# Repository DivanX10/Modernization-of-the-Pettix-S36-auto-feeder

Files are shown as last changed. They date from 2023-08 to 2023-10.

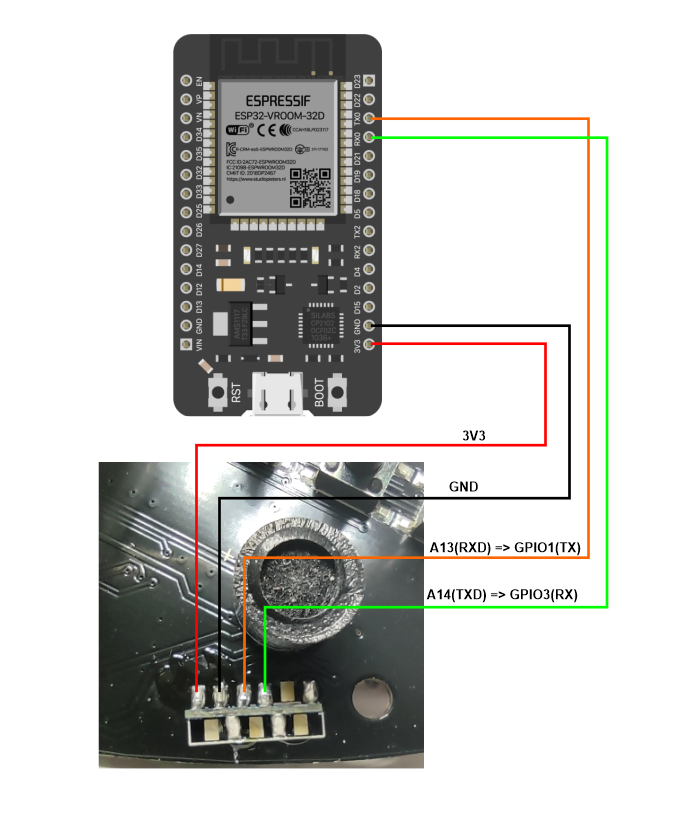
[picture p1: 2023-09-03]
images/Connect the ESP to the RX-TX feeder.png

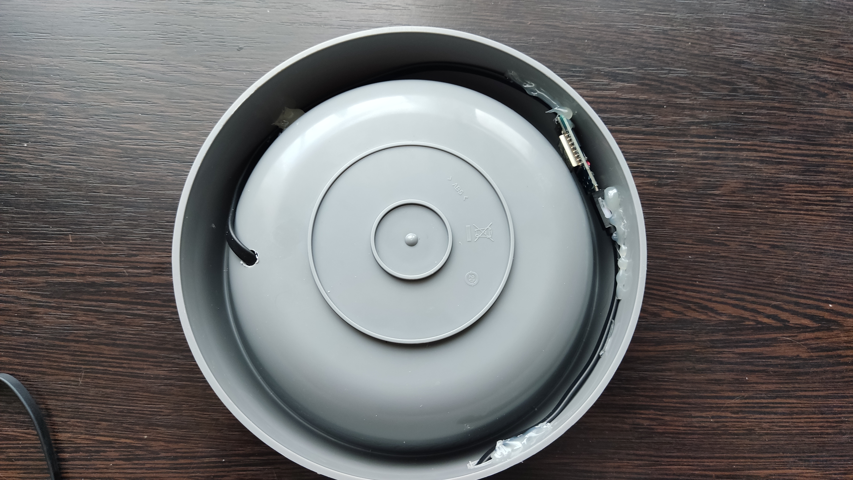
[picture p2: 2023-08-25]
images/Images 04.jpg

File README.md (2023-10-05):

### [Read in English here](https://github.com/DivanX10/cat-bowl-with-scales/blob/main/README_EN.md)

# Модернизация автокормушки Pettix S36

Проект для ESPHome и Home Assistant



***

### Смотреть видео [Автокормушка с миской на весах](https://youtu.be/qWqOF85e7Kk)
### Смотреть видео [Автокормушка с вращающейся миской на весах](https://youtu.be/ATh8qVqtzHo?si=UaMHs_tmDmoli1Qk)

***

## Отвязываем кормушку от облака Tuya и переводим на ESPHome

<details>
  <summary><b>Подключаем ESP к кормушке</b></summary>

  > Используйте платы ESP8266 и ESP32 на свое усмотрение, я использовал ESP32 по той причине, что оно у меня было свободным
 
Выпаиваем чип WBR2 и подключаем ESP. [WBR2 Module Datasheet](https://developer.tuya.com/en/docs/iot/wbr2-datasheet?id=K989h4vonmsey)





  
</details>

<details>
  <summary><b>Расшифровка протокола для управления кормушкой</b></summary>

**Включить меделенную подачу корма**
```
55:AA:00:06:00:05:06:01:00:01:01:13
```

**Выключить меделенную подачу корма**
```
55:AA:00:06:00:05:06:01:00:01:00:12
```
***

**Включить 24 часа**
```
55:AA:00:06:00:05:66:01:00:01:01:73
```

**Выключить 24 часа**
```
55:AA:00:06:00:05:66:01:00:01:00:72
```
***

**Подача порции корма**

1 порция
```
55:AA:00:06:00:08:03:02:00:04:00:00:00:01:17
```

2 порции
```
55:AA:00:06:00:08:03:02:00:04:00:00:00:02:18
```

3 порции
```
55:AA:00:06:00:08:03:02:00:04:00:00:00:03:19
```

4 порции
```
55:AA:00:06:00:08:03:02:00:04:00:00:00:04:1A
```

5 порции
```
55:AA:00:06:00:08:03:02:00:04:00:00:00:05:1B
```

6 порции
```
55:AA:00:06:00:08:03:02:00:04:00:00:00:06:1C
```

***

**Время воспроизведения голоса**

0
```
55:AA:00:06:00:08:12:02:00:04:00:00:00:00:25
```

1
```
55:AA:00:06:00:08:12:02:00:04:00:00:00:01:26
```

2
```
55:AA:00:06:00:08:12:02:00:04:00:00:00:02:27
```

3
```
55:AA:00:06:00:08:12:02:00:04:00:00:00:03:28
```

4
```
55:AA:00:06:00:08:12:02:00:04:00:00:00:04:29
```

5
```
55:AA:00:06:00:08:12:02:00:04:00:00:00:05:2A
```

6
```
55:AA:00:06:00:08:12:02:00:04:00:00:00:06:2B
```

***

**Сенсор наличия корма в баке**

В контейнере корм имеется
```
55:AA:03:07:00:05:0E:05:00:01:00:22
```

В контейнере корм закончился
```
55:AA:03:07:00:05:0E:05:00:01:01:23
```

</details>

</details>

<details>
  <summary><b>ESPHome</b></summary>

### Конфигурации смотреть [здесь](https://github.com/DivanX10/Modernization-of-the-Pettix-S36-auto-feeder/tree/main/files/ESPHome/ru)
***  
Перед тем как использовать весь код, откалибруйте свои весы. Уберите из кода эти строчки и включите журналирование в режиме DEBUG. Так мы будем получать сырые данные. Зафиксируйте вес без груза, скопируйте цифры с логов как есть, потом возъмите груз на 500 грамм и поставьте на весы, зафиксируйте цифры. Все эти цифры запишите в линейный фильтр

Пример фильтра, где `-169085` это сырое значение и это значение без груза на весах, поэтому я указал что данное значение имеет вес 0 грамм, а значение `-92230` отобразилось в логах после того, как я установил груз весом 500 грамм и после указал, что данное значение имеет вес 500 грамм
```
filters:
  - calibrate_linear:
      - -169085 -> 0
      - -92230 -> 500
```

Так выглядит код с журналированием в режиме отладки и без использования фильтра с линейной калибровкой. Это позволит вам получить сырые значения
```
#Журналирование
logger:
  level: DEBUG #Режим отладки

sensor:
  # Весы кошачьей миски
  - platform: hx711
    name: "${node_name} Weight"
    icon: mdi:scale
    id: idWeight
    dout_pin: D7 #DT
    clk_pin: D6  #SCK
    gain: 64
    update_interval: 1s
    unit_of_measurement: g
    accuracy_decimals: 0
    device_class: weight
    state_class: measurement
    entity_category: diagnostic
    internal: False
```

Если показания нестабильны, часто и сильно скачут, то смените контроллер HX711 на исправный, в противном случае фильтры не помогут. Лично сам с этим столкнулся и много времени потратил впустую на настройку фильтров. При исправном контроллере HX711 показания весов в момент покоя могут чуть-чуть меняться и это нормально, но не скачут сильно и постоянно. В таком случае дополнительный фильтр поможет, например фильтр медиана, который сможет стабилизировать показания весов. [Подробнее читаем в документации ESPHome](https://esphome.io/components/sensor/index.html#median)

```
      - median:
          window_size: 7
          send_every: 4
          send_first_at: 3
```
                
</details>

## Автокормушка с миской на весах

<details>
  <summary><b>Что нужно для сборки весов для миски</b></summary>
  
* Чувствительные тензодатчики с точностью 1 грамм. Найти можно в электронных кухонных весах с круглыми ножками. Берем любые кухонные весы с круглыми ножками, а не с палками. Это легко можно понять, если перевернуть весы. [Я брал такие кухонные весы](https://ozon.ru/t/zewBN6W)
* ESP8266 Wemos Mini D1
* Контроллер весов HX711
* Распечатать платформу. Скачать можно [здесь](https://github.com/DivanX10/cat-bowl-with-scales/tree/main/files/STL%20Scales)
</details>

<details>
  <summary><b>Фотографии</b></summary>
  





</details>

<details>
  <summary><b>Схема подключения и сборка</b></summary>

Схема подключения весов к контроллеру HX711 и к ESP8266







</details>

<details>
  <summary><b>Home Assistant</b></summary>

feeder_pettix_s36_control_panel_scales_ru

**Для работы карточки необходимо установить компоненты**
* [Fold Entity Row](https://github.com/thomasloven/lovelace-fold-entity-row)
* [Multiple Entity Row](https://github.com/benct/lovelace-multiple-entity-row)

**Карточка и шаблоны**
* Код карточки можно взять [здесь](https://github.com/DivanX10/Modernization-of-the-Pettix-S36-auto-feeder/blob/main/files/HomeAssistant/ru/Карточка.%20Миска%20с%20весами.yaml)
* Код шаблона можно взять [здесь](https://github.com/DivanX10/Modernization-of-the-Pettix-S36-auto-feeder/blob/main/files/HomeAssistant/ru/Шаблон.yaml)
  
</details>

<details>
  <summary><b>3D модель</b></summary>
  
Платформу спроектировал в программе FreeCAD. Скачать FreeCAD [можно здесь](https://www.freecad.org/?lang=ru). Я вложил 3 файла, два файла STL и один для FreeCAD, где вы сможете отредактировать при необходимости. Я спроектировал так, чтобы тензодатчики держались крепко и сделал клипсы в виде дуги из-за чего тензодатчики с трудом встают на свои места, нужно тоненькой плоской отверткой поддеть, но зато стоят четко и очень трудно их будет демонтировать без повреждения корпуса.

Готовые модели можно скачать [здесь](https://github.com/DivanX10/Modernization-of-the-Pettix-S36-auto-feeder/tree/main/files/STL%20Scales)



</details>

## Автокормушка с вращающейся миской с весами

<details>
  <summary><b>Что нужно для сборки вращающейся миски с весами</b></summary>
  
* Чувствительные тензодатчики с точностью 1 грамм. Найти можно в электронных кухонных весах с круглыми ножками. Берем любые кухонные весы с круглыми ножками, а не с палками. Это легко можно понять, если перевернуть весы. [Я брал такие кухонные весы](https://ozon.ru/t/zewBN6W)



* ESP8266 Wemos Mini D1
* Контроллер весов HX711
* Модуль драйвера ULN2003 и шаговый двигатель 28YBJ 48
* Модуль часов реального времени (RTS) DS1307
* Подшипник 6814 2RS (61814) SLZ. Брал [здесь](https://ozon.ru/t/6M8ZB3Y)
  * Внешний диаметр: 90 мм
  * Внутренний диаметр: 70 мм
  * Высота: 10 мм


* Жидкая резина KUDO COLOR FLEX, Прозрачная. Брал [здесь](https://ozon.ru/t/wz6gR7n)
  


* Распечатать миску и платформу. Скачать можно [здесь](https://github.com/DivanX10/Modernization-of-the-Pettix-S36-auto-feeder/tree/main/files/STL%20Rotating%20bowl%20with%20scales)

</details>

<details>
  <summary><b>Фотографии</b></summary>
  








</details>

<details>
  <summary><b>Cхема подключения</b></summary>

Питание берем от самой автокормушки, которое выдает 5V и 1A, чего будет достаточно, чтобы запитать всю кормушку полностью. Для полной работы кормушки требуется сила тока до 800мА

Connection diagram 01

</details>

<details>
  <summary><b>Home Assistant</b></summary>

feeder_pettix_s36_control_panel_ru

**Для работы карточки необходимо установить компоненты**
* [History explorer card](https://github.com/alexarch21/history-explorer-card)
* [Button Card](https://github.com/custom-cards/button-card)

**Карточка и шаблоны**
* Код карточки можно взять [здесь](https://github.com/DivanX10/Modernization-of-the-Pettix-S36-auto-feeder/blob/main/files/HomeAssistant/ru/Карточка.%20Вращающаяся%20миска%20с%20весами.yaml)
* Код шаблона можно взять [здесь](https://github.com/DivanX10/Modernization-of-the-Pettix-S36-auto-feeder/blob/main/files/HomeAssistant/ru/Шаблон.yaml)

</details>

<details>
  <summary><b>3D модель</b></summary>

Миска состоит из нескольких деталей. Сделано для экономии времени печати и филамента на случай, если деталь сломалась и чтобы не печатать всю миску целиком заново. Про подшипник 6814 2RS (61814) SLZ читаем ниже 

Готовые модели можно скачать [тут](https://github.com/DivanX10/Modernization-of-the-Pettix-S36-auto-feeder/tree/main/files/STL%20Rotating%20bowl%20with%20scales)



> Оранжевый круг, это подшипник 6814 2RS (61814) SLZ, который вставляется в круглую платформу под стальную миску (на скриншоте синего цвета). Чтобы стальная миска не скользила на верхней части платформы, рекомендую сделать напыление жидкой резиной. Получается отличное сцепление с миской



</details>

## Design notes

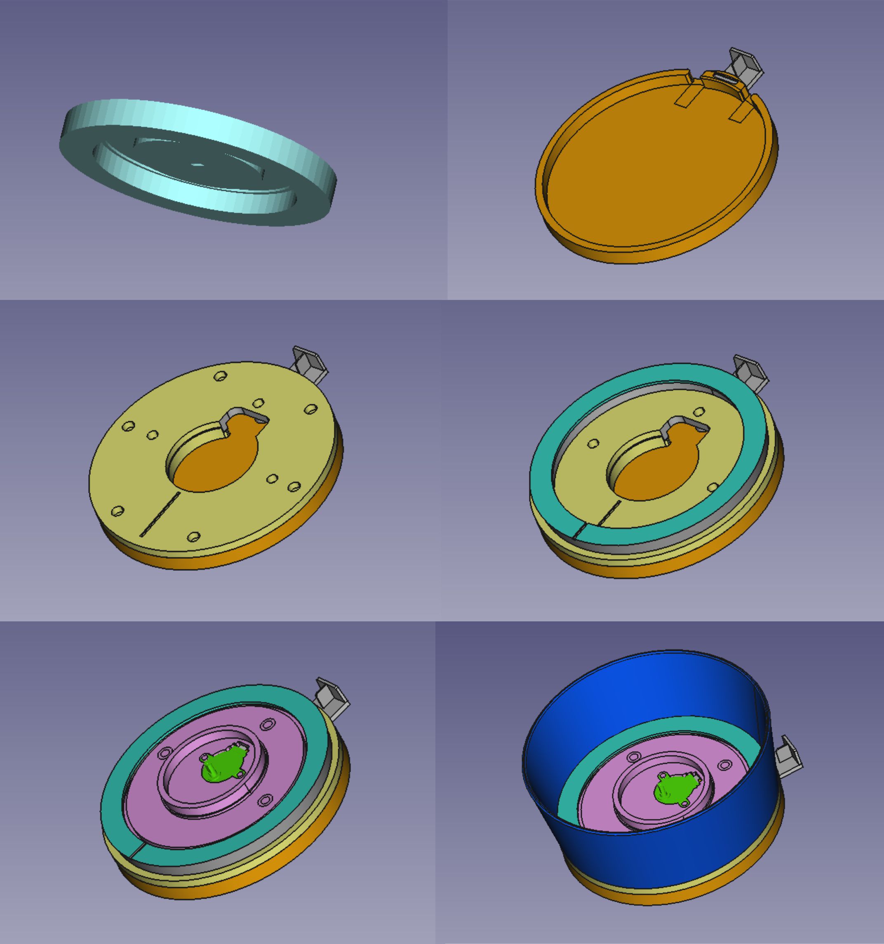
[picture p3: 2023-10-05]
images/3d model rotating bowl with scales 01.jpg

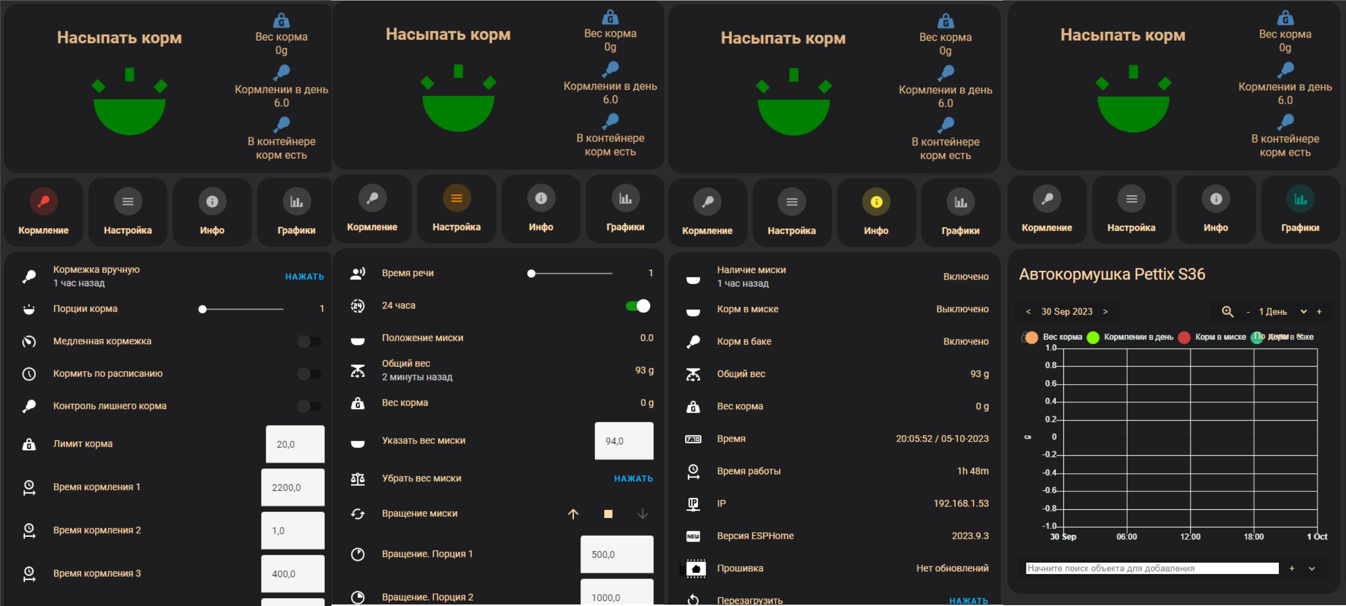
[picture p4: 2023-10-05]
images/feeder pettix s36 control panel rotating bowl with scales ru.jpg

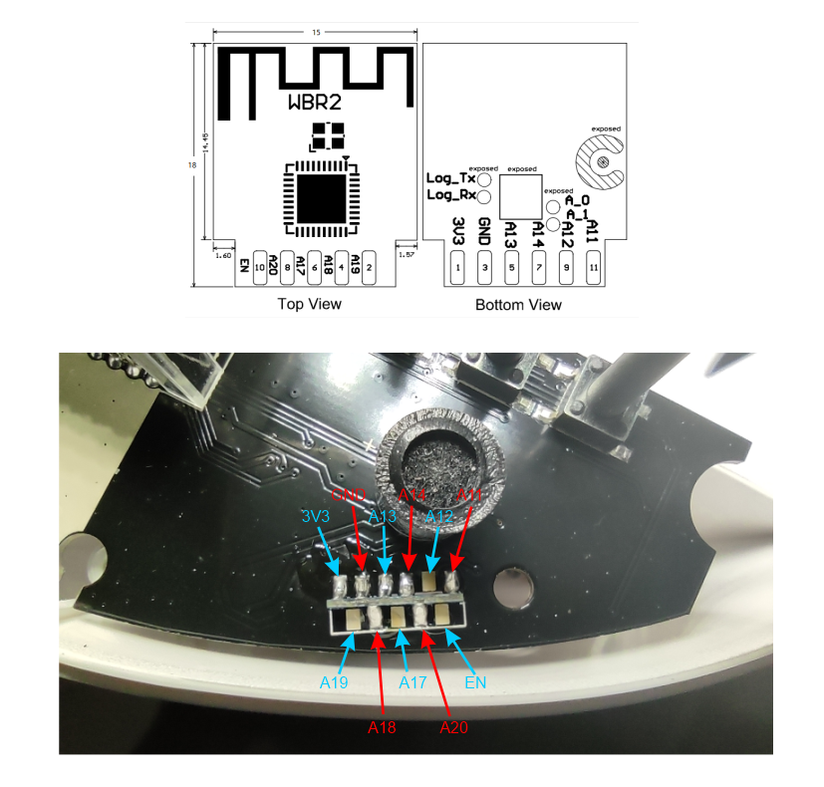
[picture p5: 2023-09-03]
images/Images 07.png

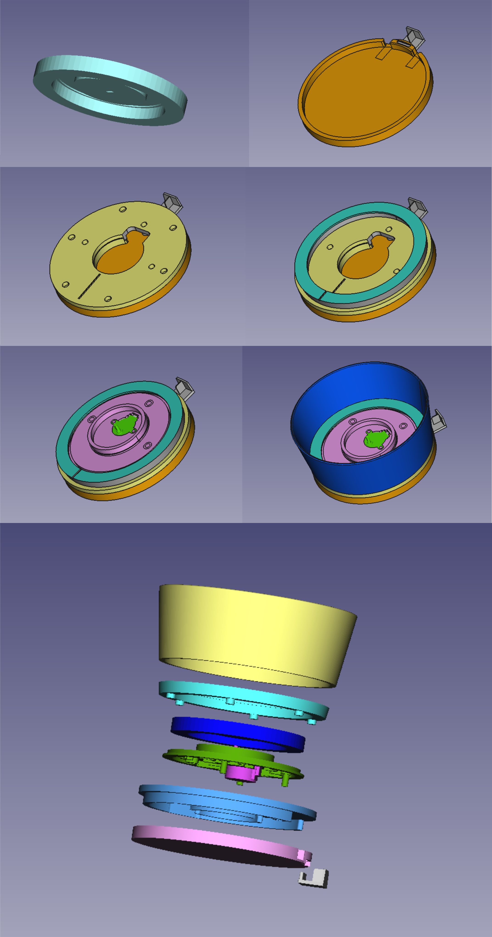
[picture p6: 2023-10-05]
images/3d model rotating bowl with scales.jpg

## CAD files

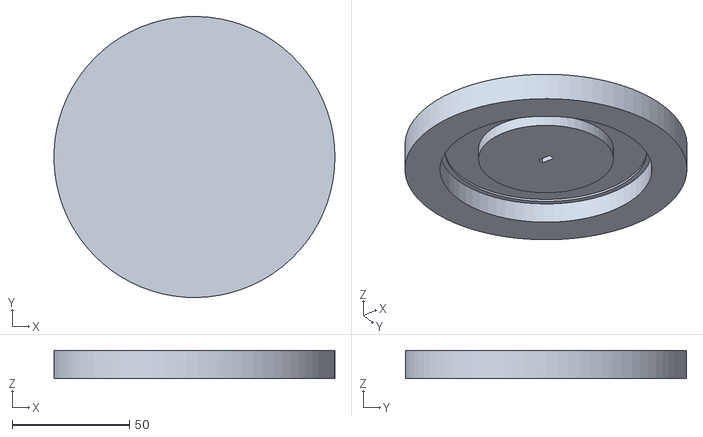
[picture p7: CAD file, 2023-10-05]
files/STL Rotating bowl with scales/08 Upper platform for bowl and bearing (Print 1 piece).stl
120.0 x 120.0 x 12.0

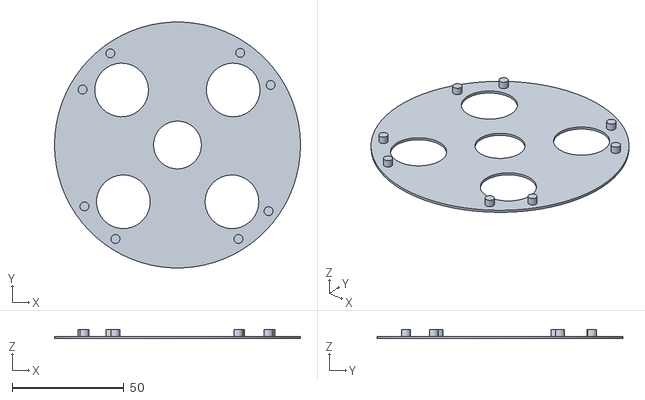
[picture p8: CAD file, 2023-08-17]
files/STL Scales/Cap.stl
110.0 x 109.9 x 4.10

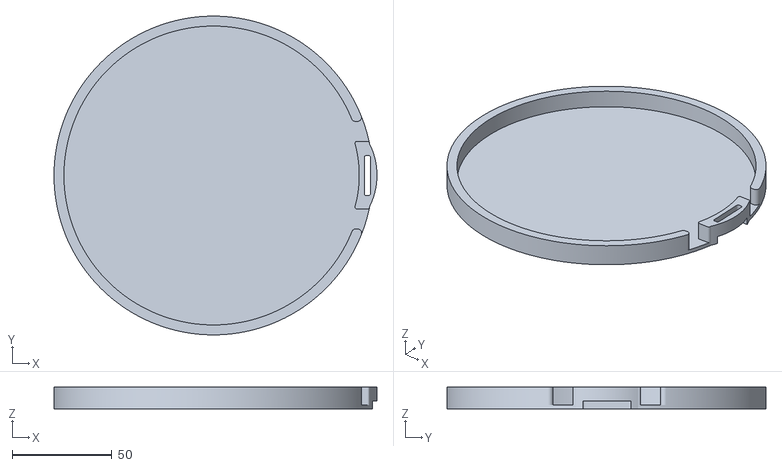
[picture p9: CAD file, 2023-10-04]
files/STL Rotating bowl with scales/05 Lower cover for the middle platform (Print 1 piece).stl
162.1 x 160.0 x 11.0

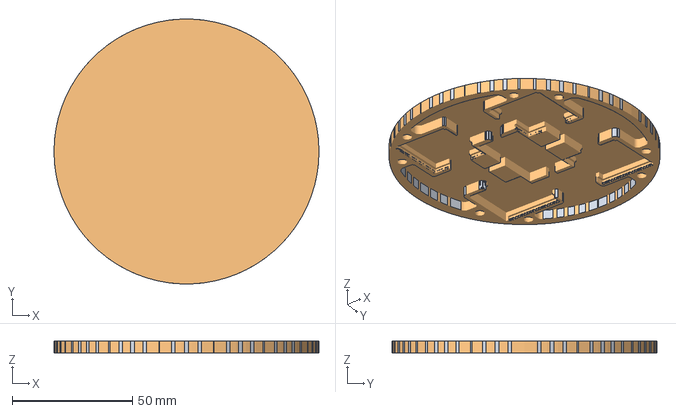
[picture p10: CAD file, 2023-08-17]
files/STL Scales/Platform for a bowl.FCStd
110.0 x 110.0 x 5.00 mm
Круглая платформа005
Круглая платформа005 (Meshed)

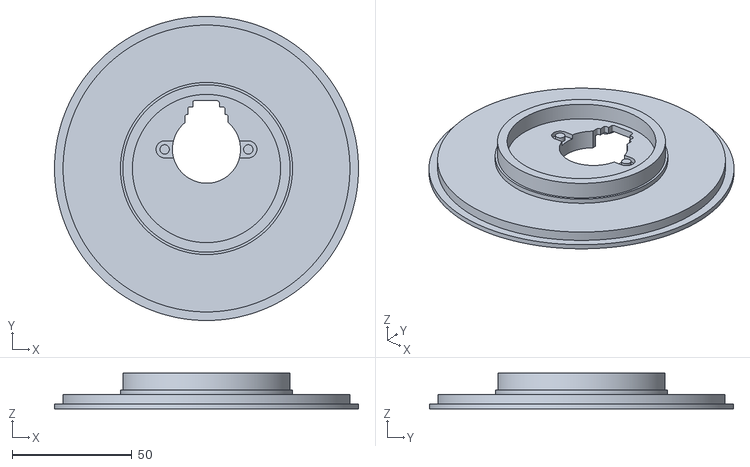
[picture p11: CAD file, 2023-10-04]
files/STL Rotating bowl with scales/03 Platform with scales and motor (Print 1 piece).stl
127.2 x 127.2 x 15.0

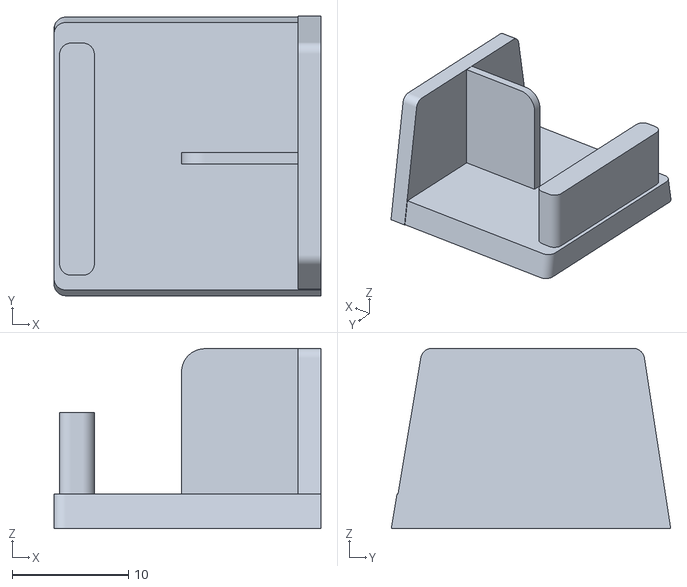
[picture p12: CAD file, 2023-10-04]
files/STL Rotating bowl with scales/06 Feeder bowl holder (Print 1 piece).stl
23.0 x 24.1 x 15.5

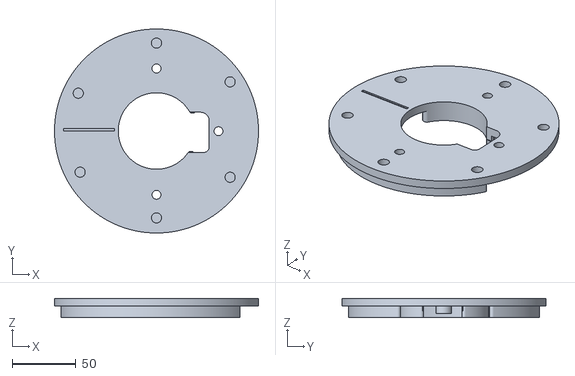
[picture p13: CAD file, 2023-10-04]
files/STL Rotating bowl with scales/04 Medium platform for a platform with weights (Print 1 piece).stl
160.0 x 160.0 x 15.0

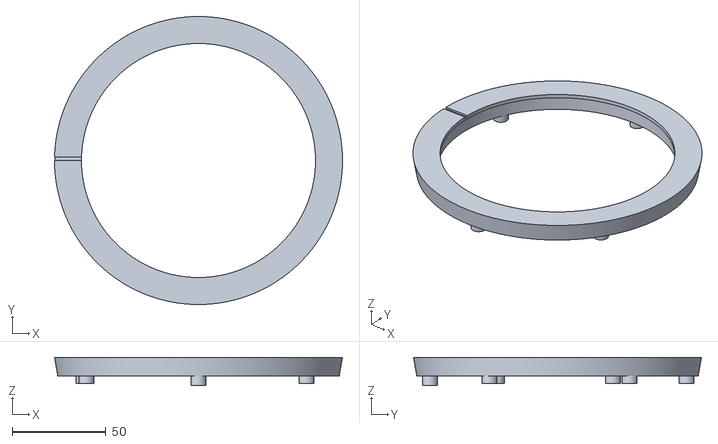
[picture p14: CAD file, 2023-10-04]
files/STL Rotating bowl with scales/02 Lock with axes for the upper body and platform with scales (Print 1 piece).stl
153.9 x 153.9 x 15.0

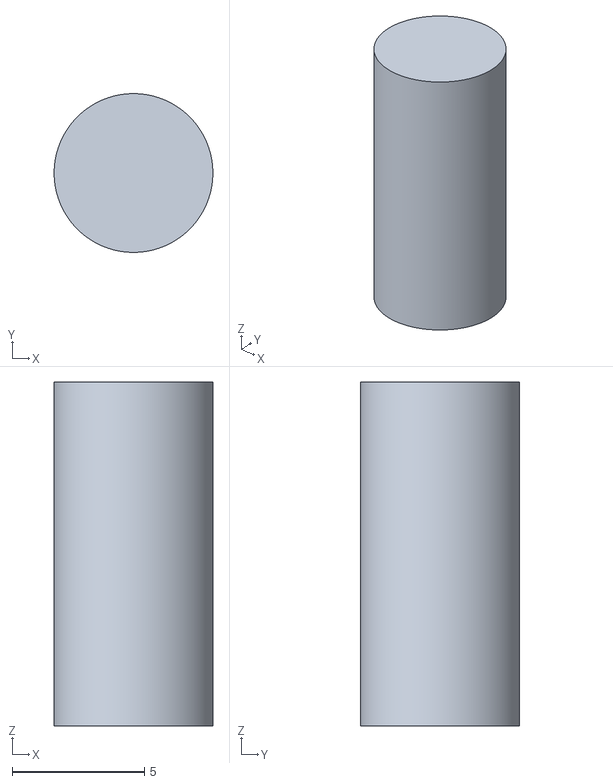
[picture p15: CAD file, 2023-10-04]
files/STL Rotating bowl with scales/07 Cylinder (Print 3 pieces).stl
6.00 x 6.00 x 13.0

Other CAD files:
files/STL Scales/Platform for a bowl.stl

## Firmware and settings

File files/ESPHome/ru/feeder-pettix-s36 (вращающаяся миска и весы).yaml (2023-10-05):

#####################################################################################
##################################### Переменные ####################################
substitutions:
  board_name: ESP Feeder Pettix S36
  node_name: feeder pettix s36
  max_skipped_time: "60" #Минуты, в течение которых будем запускать пропущенную кормежку

#####################################################################################
################################ Основная конфигурация ##############################
esphome:
  name: feeder-pettix-s36
  friendly_name: feeder-pettix-s36
  comment: WeMos D1 Feeder Pettix S36
  on_boot:
    then:
      #Считаем время RTC один раз при загрузке системы.
      ds1307.read_time:

#####################################################################################
###################################### Платформа ####################################
esp8266:
  board: d1_mini
  framework:
    version: recommended
  #Сохраняем предустановленные настройки. После перезагрузки настройки не сбрасываются  
  restore_from_flash: true

#Сброс данных на флэш-накопитель для уменьшения износа флеш-накопителя
preferences:
  flash_write_interval: 1min

#####################################################################################
################################ Wi-Fi и точка доступа ##############################
#Учетные данные Wi-Fi для подключения платы к домашней сети
wifi:
  ssid: !secret wifi_ssid
  password: !secret wifi_password
  id: idWiFi
  fast_connect: off
  reboot_timeout: 5min

#Если не будет связи с WiFi, то поднимется точка доступа
  ap:
    ssid: ESP Feeder S36 Tuya
    password: !secret ap_esp_password
    ap_timeout: 1 min
    manual_ip:
      static_ip: 192.168.4.1
      gateway: 192.168.4.1
      subnet: 255.255.255.0

#Компонент mdns заставляет узел объявлять о себе в локальной сети, используя протокол многоадресной рассылки DNS (mDNS), по умолчанию для mDNS disabled: false
mdns:
  disabled: false

#Компонент captive portal в ESPHome является резервным механизмом на случай сбоя подключения к настроенному Wi-Fi
captive_portal:

#Веб сервер
web_server:
  port: 80

#Журналирование
logger:
  level: ERROR #DEBUG
  baud_rate: 0

#Enable Home Assistant API
#Шифрование выключил
api:

#Обновление по воздуху (OTA)
ota:
  password: "esphome"

#####################################################################################
######################################### UART ######################################
uart:
  tx_pin: GPIO1 #белый провод
  rx_pin: GPIO3 #зеленый провод
  baud_rate: 9600
  stop_bits: 1
  data_bits: 8
  parity: NONE

#Включить компонент Tuya MCU
tuya:
  time_id: homeassistant_time
  on_datapoint_update:
    - sensor_datapoint: 14
      datapoint_type: bitmask
      then:
        lambda: |-
          std::bitset<4> probes(x);
          probes.flip();
          id(idFoodLevel).publish_state(probes.test(0));

#####################################################################################
########################### Глобальные переменные ###################################
globals:
#Последняя кормежка по расписанию
  - id: last_manual_feed_ts
    type: int
    restore_value: yes
    initial_value: '2147483648'

  - id: idWeightBowlGlobal
    type: int
    restore_value: yes
    initial_value: '0'

#####################################################################################
############################# Платформа вывода ######################################
#Шаговый мотор 28BYJ-48
stepper:
  - platform: uln2003
    id: idStepperMotor
    pin_a: D5
    pin_b: D6
    pin_c: D7
    pin_d: D8
    max_speed: 250 steps/s
    sleep_when_done: True
    step_mode: FULL_STEP

    #Опционально:
    acceleration: inf
    deceleration: inf

#Модуль часов реального времени (RTS) на базе микросхемы DS1307
i2c:
  sda: D1 #синий провод
  scl: D2 #зеленый провод
  scan: true
  id: ds1307_time

#####################################################################################
################################## Выключатель ######################################
switch:
#Медленная подача корма
  - platform: template
    name: "Slow Feed"
    icon: mdi:speedometer-slow
    optimistic: true
    restore_mode: RESTORE_DEFAULT_OFF
    turn_on_action:
      - uart.write: [0x55, 0xAA, 0x00, 0x06, 0x00, 0x05, 0x06, 0x01, 0x00, 0x01, 0x01, 0x13]
    turn_off_action:
      - uart.write: [0x55, 0xAA, 0x00, 0x06, 0x00, 0x05, 0x06, 0x01, 0x00, 0x01, 0x00, 0x12]

#Отображение на часах 12/24 часовой формат времени 
  - platform: template
    name: "24 Hours"
    icon: mdi:hours-24
    optimistic: true
    restore_mode: RESTORE_DEFAULT_ON
    turn_on_action:
      - uart.write: [0x55, 0xAA, 0x00, 0x06, 0x00, 0x05, 0x66, 0x01, 0x00, 0x01, 0x01, 0x73]
    turn_off_action:
      - uart.write: [0x55, 0xAA, 0x00, 0x06, 0x00, 0x05, 0x66, 0x01, 0x00, 0x01, 0x00, 0x72]
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

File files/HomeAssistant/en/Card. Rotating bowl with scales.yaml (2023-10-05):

#Pay attention to entity. Your object names may differ from this example. List your objects

type: vertical-stack
cards:
  - square: false
    columns: 1
    type: grid
    cards:
      - type: horizontal-stack
        cards:
          - type: custom:button-card
            entity: binary_sensor.feeder_pettix_s36_bowl
            tap_action:
              action: call-service
              service: button.press
              target:
                entity_id: button.feeder_pettix_s36_feed
            hold_action:
              action: none
            double_tap_action:
              action: none
            state:
              - value: 'on'
                color: green
              - value: 'off'
                color: red
            icon: mdi:wall-sconce-round-variant
            name: |
              [[[
                if (entity.state == "on")
                  return "Pour in food";
                if (entity.state == "off")
                  return "No bowl";
              ]]]
            color: SteelBlue
            styles:
              card:
                - padding: 1%
                - color: ivory
                - font-size: 10px
                - height: 250px
              grid:
                - grid-template-areas: '"i icon" "n icon" "n weight_food" "n day" "n status" '
                - grid-template-columns: lfr lf
                - grid-template-rows: lfr min-content min-content
              name:
                - font-size: 25px
                - color: BurlyWood
                - font-weight: bold
                - padding-bottom: 180px
                - justify-self: center
              img_cell:
                - justify-content: end
                - margin: none
                - margin-top: '-10%'
                - grid-row: 1 / span 6
              icon:
                - width: 300px
                - height: 160px
                - margin-top: 2%
                - top: 65px
              custom_fields:
                weight_food:
                  - justify-self: center
                  - margin-top: '-20%'
                  - height: 70px
                  - width: 150px
                  - font-size: 16px
                  - line-height: 20px
                  - color: BurlyWood
                day:
                  - justify-self: center
                  - margin-top: 5%
                  - height: 70px
                  - width: 150px
                  - font-size: 16px
                  - line-height: 20px
                  - color: BurlyWood
                status:
                  - justify-self: center
                  - margin-top: 5%
                  - height: 80px
                  - width: 150px
                  - font-size: 16px
                  - line-height: 20px
                  - color: BurlyWood
            custom_fields:
              weight_food: |
                [[[
                  return `<ha-icon icon="mdi:weight-gram" style="width: 50px; height: 30px; color: SteelBlue;">
                  </ha-icon><br>Feed weight<br><span>${states['sensor.feeder_pettix_s36_weight_food'].state}</span>g<p>`
                ]]]
              day: |
                [[[
                  return `<ha-icon icon="mdi:food-drumstick" style="width: 50px; height: 30px; color: SteelBlue;">
                  </ha-icon><br>Feeding per day<br><span>${states['sensor.feeder_pettix_s36_feeding_per_day'].state}</span><p>`
                ]]]
              status: |
                [[[
                  if (states['binary_sensor.feeder_pettix_s36_food_level'].state == 'on')
                  return  `<ha-icon icon="mdi:food-drumstick" style="width: 50px; height: 30px; color: SteelBlue;">
                  </ha-icon><br>In a container<br><span>there is food</span>`
                  
                  return  `<ha-icon icon="mdi:food-drumstick-off" style="width: 50px; height: 30px; color: red;">
                  </ha-icon><br>In a container<br><span>ran out of food</span>`
                ]]]
      - type: horizontal-stack
        cards:
          - type: custom:mushroom-entity-card
            entity: input_boolean.feeder_pettix_s36_control_panel_1
            tap_action:
              action: toggle
            icon_color: red
            name: Feeding
            secondary_info: none
            icon: mdi:food-drumstick
            fill_container: false
            layout: vertical
          - type: custom:mushroom-entity-card
            entity: input_boolean.feeder_pettix_s36_control_panel_2
            name: Settings
            tap_action:
              action: toggle
            secondary_info: none
            layout: vertical
            icon: mdi:menu
            icon_color: orange
          - type: custom:mushroom-entity-card
            name: Info
            tap_action:
              action: toggle
            secondary_info: none
            layout: vertical
            entity: input_boolean.feeder_pettix_s36_control_panel_3
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
